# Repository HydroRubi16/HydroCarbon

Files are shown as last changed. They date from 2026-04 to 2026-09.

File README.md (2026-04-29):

# HydroCarbon
This is my custom built 4040/4020 Trident. I will update this over the next few weeks with all my files I used to build my printer..

<!--<img src="https://github.com/HydroRubi16/HydroCarbon/blob/main/images/Trident%20Doom%20front%20angle.png">  -->

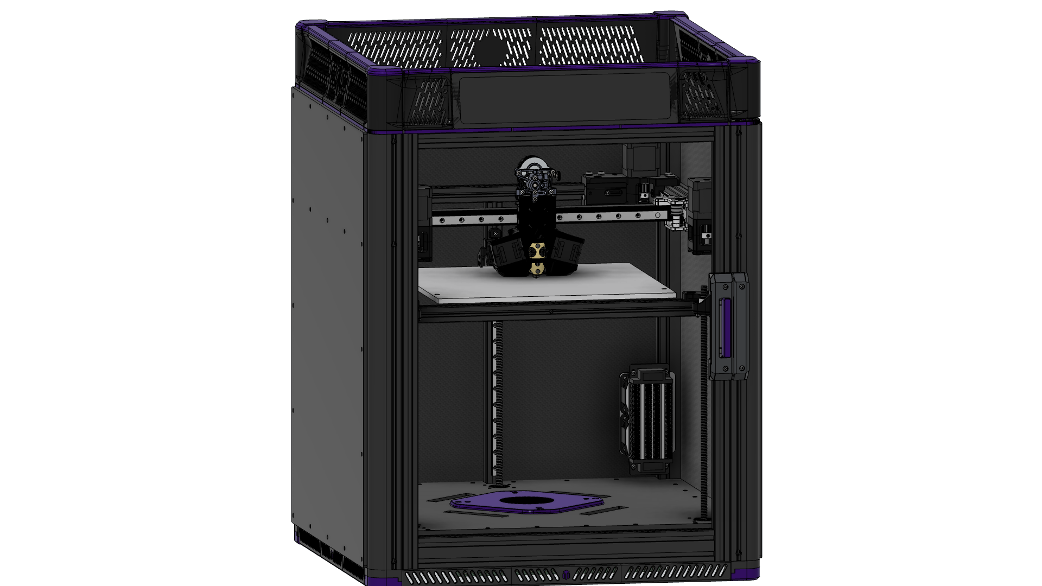
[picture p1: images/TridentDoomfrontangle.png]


This is my latest build, based on all the things I have learned from other builds. I really wanted to build a higher performance printer that looks good. In using the stock extrusion lengths you ‘lose’ 20mm going with 4040 extrusions and 28mm with Trinity, which is why I’m using the 300 Cube length corners (550mm) with standard 300mm lead screw steppers — this should still allow me 250mm Z travel (Actually 238mm right now..). I drilled additional hole in the round corners to allow 3 fasters to be used with 4040 sides and back. For the panels there will be a stack of 3.5mm carbon fiber, 10mm adhesive foam insulation, 5mm structurer panel. Yes, carbon fiber is a bit crazy here, but I got a killer deal on 3.5mm … apparently no one uses it, so it was cheaper than PC panels.

**Frame:**  
Trident Doom corners by LDO (300 Cube)  
4040 on bottom sides/back  
2040 on top and bottom front  
Dual 2040 on Y  
Corner braces wherever possible  

**Gantry:**  
Printed Monolith AWD 10mm (3DXTech EZPCCF)  
(Like everyone else, I’m going CNC as soon as it’s available)  
Sheet metal XY Joints  
Carbonara X Beam  
West3D Berserker hybrid ceramic bearings  
10mm EDPM closed loop belts  

**Toolhead:**  
Trinity modded for 10mm belts  
Chube Compact  
Sherpa Mini  

**Motors:**  
LDO-42STH48-2504AH(S45R)  
LDO-42STH40-1684L300E  

**Rails:**  
BST for Z  
Hiwin for Y  
Airtac for X  
GPL-226 Lube  

**Electronics:**  
Octopus Max EZ MCU  
EZ5160RGB drivers for X/Y  (48v)  
EZ2209 drivers for Z  (24v)  
Dragon Dinghy expansion board  
Waveshare USB Hub  
Phoenix Contact distribution block  
Spicy Meatball 500W heater  

**Skirts:**  
Top skirts - [Darkmatter Skirts](https://github.com/MasturMynd/Doom-Stuff/tree/main/Darkmatter-Skirts)  
Short skirts on the bottom by Brazuka and Komikaze

**Panels and insulation:**  
4.7mm structure panels on Sides/Back  
6.3mm bottom panel with motor mounts and integrated filter  
ACM top plate  
10mm and 15mm adhesive foam insulation  
3.5mm carbon fiber panels for interior  

**Goal: Gucci as fuck**

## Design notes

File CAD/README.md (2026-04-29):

# CAD coming soon......

## Frame BOM
LDO Trident DoomCube Corner Kit (300 cubed)  

| Misumi Part Number | Quantity | Location |
| --- | --- | --- |
| HFSB5-4040-420 | 3 | bottom sides/bottom back |
| HFSB5-2040-420 | 6 | top sides/top back/bottom front/Y |
| HFSB5-2020-420 | 2 | top front/bed mount |
| HFSB5-2020-360 | 1 | Z vertical |
| HFSB5-2020-290 | 1 | rear gantry |
| HFSB5-2020-282 | 1 | bed mount |
| HFSB5-2020-378 | 1 | door top |
| HFSB5-2040-378 | 1 | door bottom |
| HFSB5-2020-550 | 2 | door uprights |

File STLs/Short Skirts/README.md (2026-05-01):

# Short Skirts
Because who doesn't love short skirts?  
by Brazuka and Komikaze  

These Skirts are made exclusively for 300 Tridents or similar machines, with rounded vertical corners and top mounted electronics. You could definitely adapt other feet
to the design, but it's inteded to be used with [Hula Feet](https://github.com/thrutheframe/HULA_Voron/tree/main) (using the Switchwire plate). This can be used with either a RGB strip light or Disco on a stick. There are files for 10mm and 12mm strip lights, so choose which one fits your application. The center short skirt has the ability to also insert a neopixel. Inserts can be omitted, or printed in clear PETG or ABS, or some prefer white PLA.  
  
The feet have passage ways for running wiring up the LDO rounded corners; Please use PET sleeving for your wiring. It will rattle arround like a MF'r if you don't. 

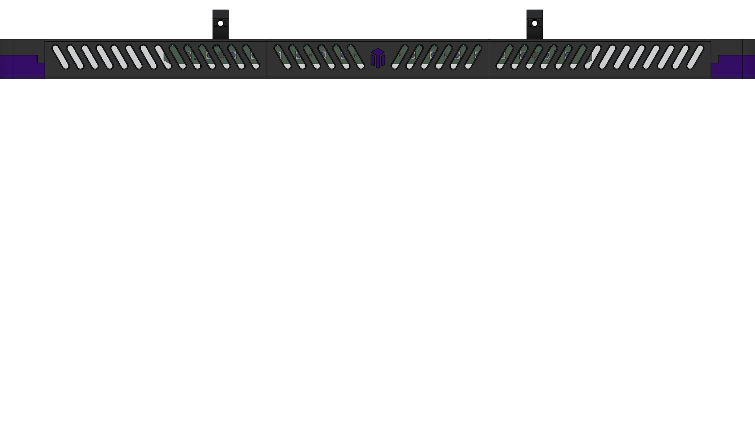
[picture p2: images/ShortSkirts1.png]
  

CAD coming sooooon...

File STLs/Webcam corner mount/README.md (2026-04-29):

# Trident corner mount web cam  

This is my web cam mount design I created for my Trident build. It's made for the Arducam, or anything of similar size-
https://www.amazon.com/dp/B0829HZ3Q7?ref_=ppx_hzsearch_conn_dt_b_fed_asin_title_7

There is a channel on the outside of the perimeter for running chamber light wiring or thermistors. The larger diameter hole is for running wiring to a top mounted electronics bay. The Cam holder is attached to the cam corner mount via 2x m3 heatserts and appropriate fasteners.

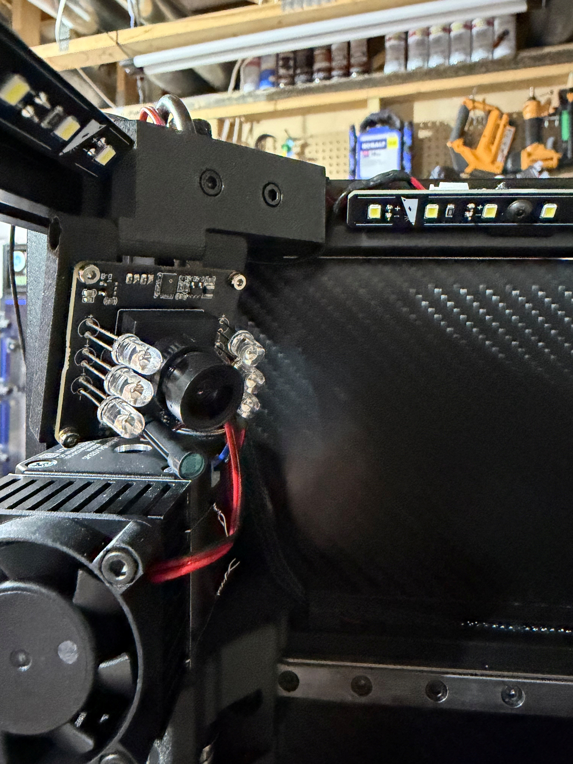
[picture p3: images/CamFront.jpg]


and a view from the top....  
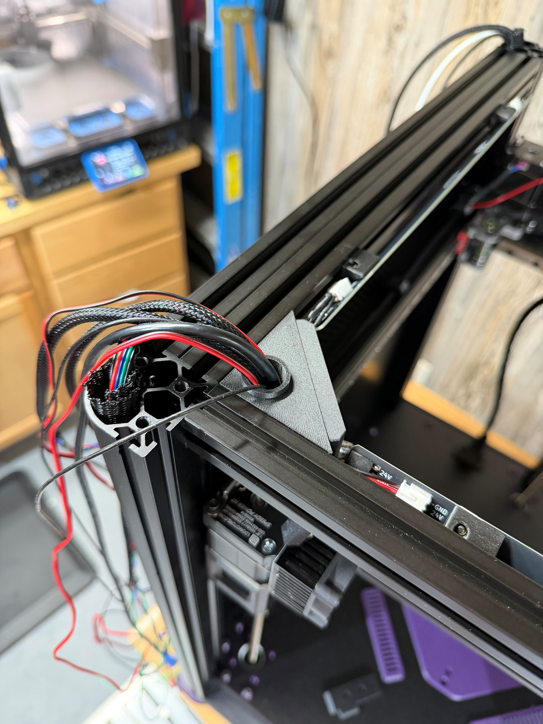
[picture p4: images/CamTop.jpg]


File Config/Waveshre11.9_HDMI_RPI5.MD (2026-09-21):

# How to install an 11.9" Waveshare HDMI display with an RPI5 using Klipperscreen
  
1. Install the HDMI screen, attach USB power, USB Touch, and HDMI to the first HDMI port (closest to USB-C)  
  
2. SSH into the PI  
```
sudo nano /boot/firmware/cmdline.txt
```  

add the following at the very end:  

```
video=HDMI-A-1:1480x320@60,rotate=90
```
	
3. Install Klipperscreen. When prompted for x11 or Wayland, choose W for Wayland  
  
4. Klipperscreen installs Cage, and I could only get Weston to work, so uninstall Cage and install Weston:  
	Uninstall Cage:  
```
sudo systemctl stop KlipperScreen
```

```
sudo apt remove cage
```

Install Weston:  

```
sudo apt install Weston seatd
```

5. Verify HDMI port and connection status  

```
grep -H . /sys/class/drm/card*-*/status | grep :connected
```

Should look like:```/sys/class/drm/card1-HDMI-A-1/status:connected```
		
6. Update INI file  
	
```
sudo nano ~/.config/weston.ini
```
	
Add the following:  

```
[output]  
name=HDMI-A-1  
transform=rotate-90
```

7. Reboot. Klipperscreen should be oriented correctly. Changing the rotating in the Weston.ini file also appears to change the touch overlay, as well.  
```
sudo reboot
```

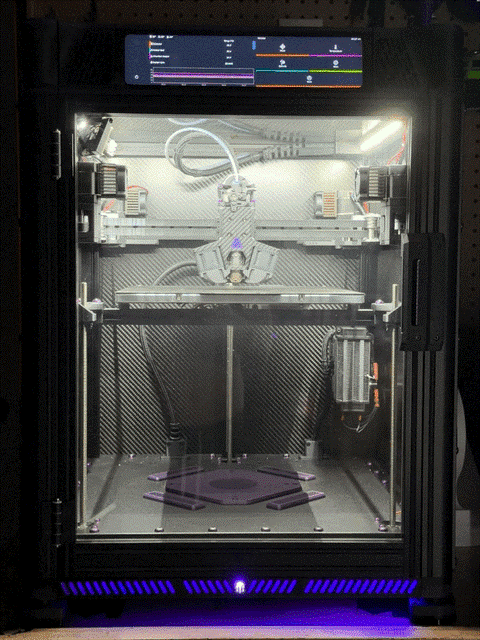
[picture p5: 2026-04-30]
images/HydroCarbon.gif

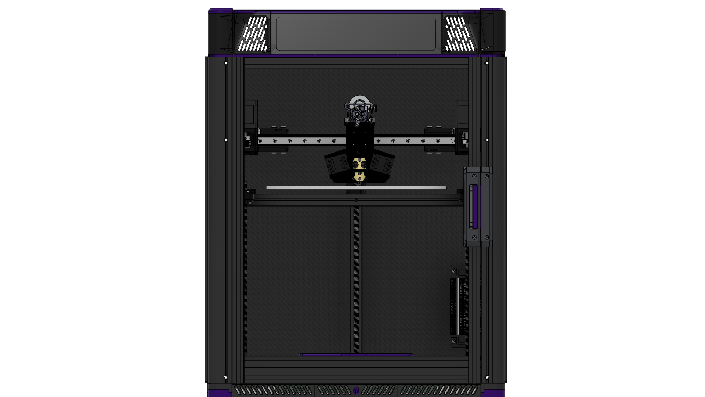
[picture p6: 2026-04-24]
images/TridentDoom.png

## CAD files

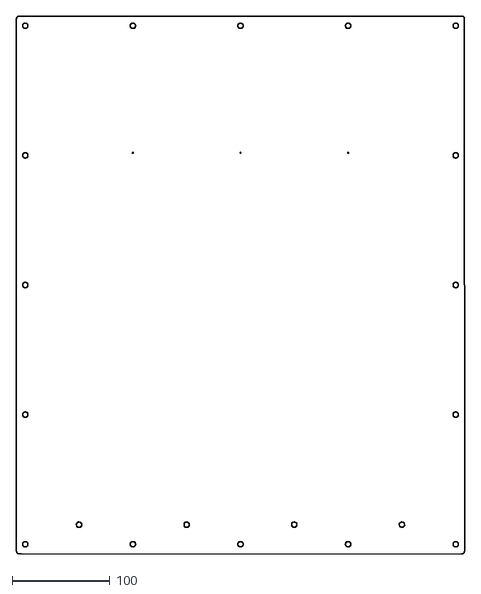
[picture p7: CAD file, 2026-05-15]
DXFs/Side_back_panel_small_hole_minus1.dxf
458.0 x 550.0

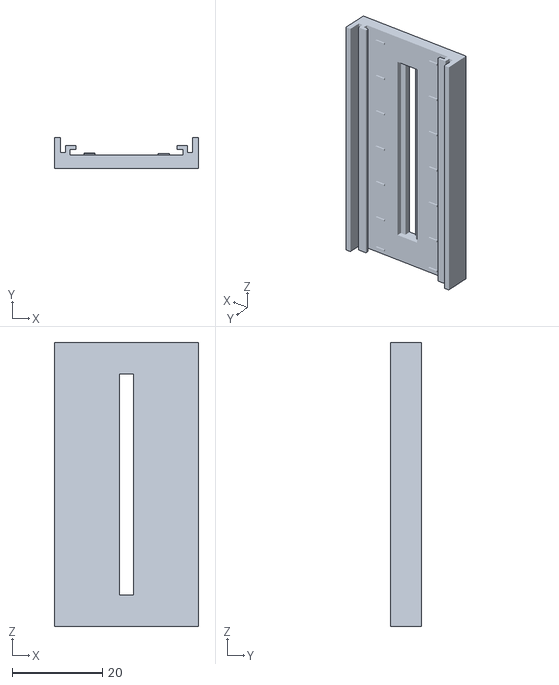
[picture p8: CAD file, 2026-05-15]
STLs/EMS Mounts/PTFIX_DC_EMS.stl
32.0 x 6.99 x 63.0

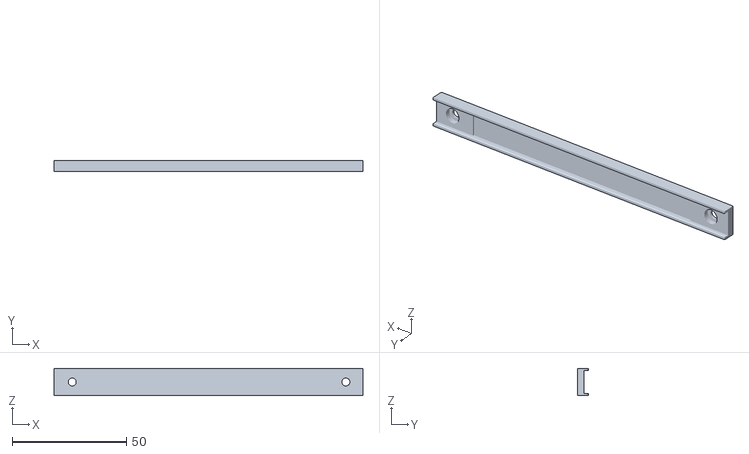
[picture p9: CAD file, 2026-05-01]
STLs/Short Skirts/StripHolder10mm.stl
135.5 x 5.00 x 12.0

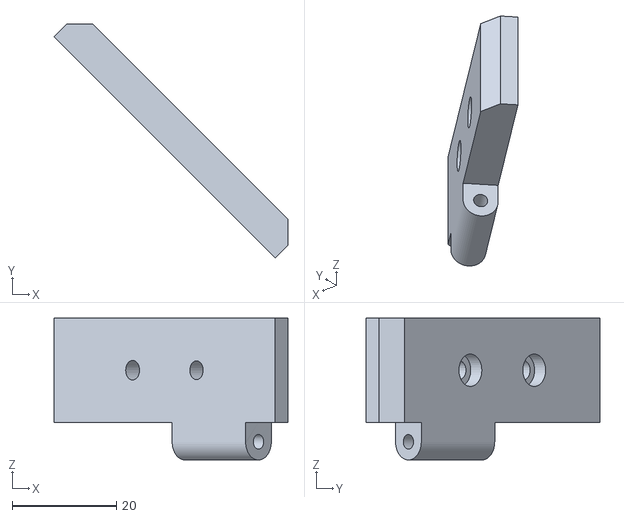
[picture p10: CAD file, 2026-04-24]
STLs/Webcam corner mount/cam holder.stl
44.8 x 44.8 x 27.2

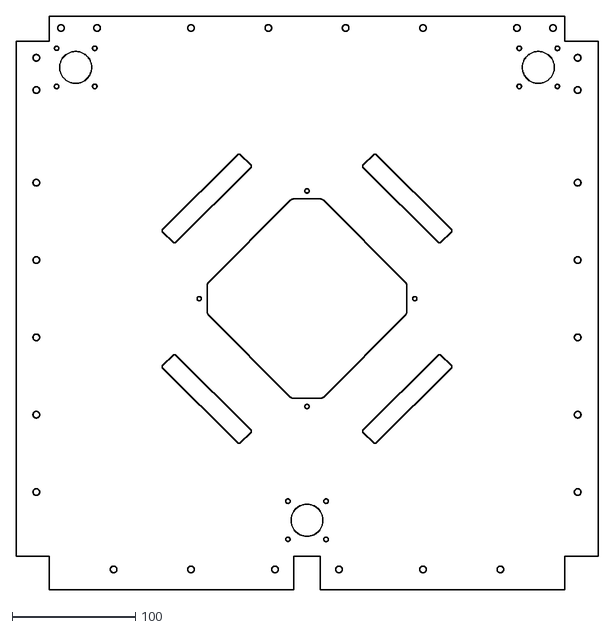
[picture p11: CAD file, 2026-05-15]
DXFs/Trident bottom panel with filter.dxf
473.0 x 466.0

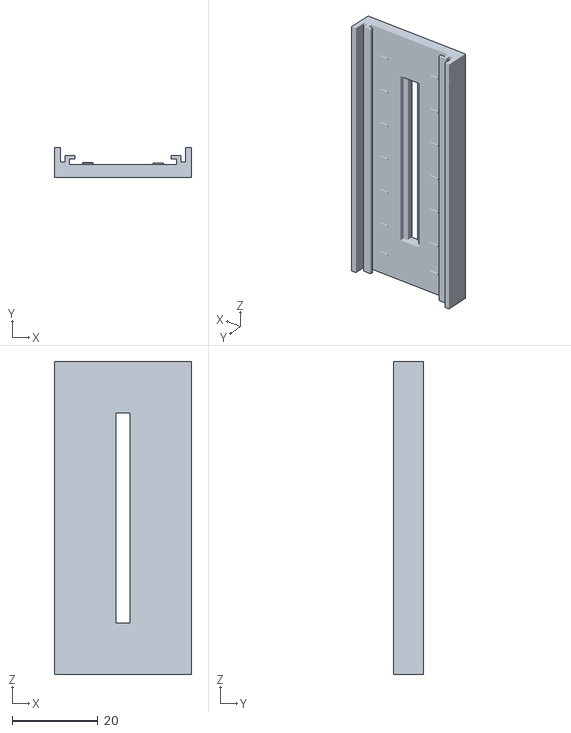
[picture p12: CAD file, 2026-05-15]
STLs/EMS Mounts/PTFIX_120v_EMS.stl
32.0 x 6.99 x 73.0

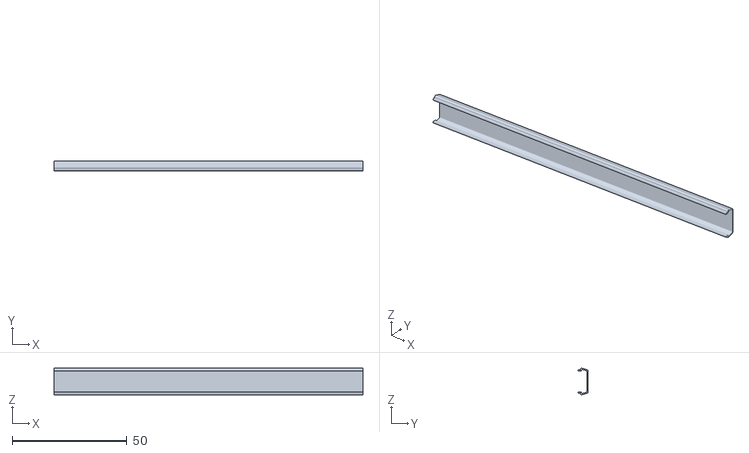
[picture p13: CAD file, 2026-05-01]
STLs/Short Skirts/StripDiffuser10mm.stl
134.5 x 4.32 x 11.7

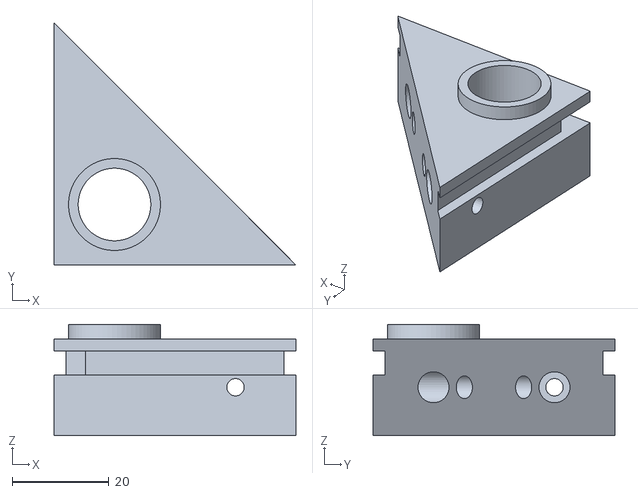
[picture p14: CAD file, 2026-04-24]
STLs/Webcam corner mount/cam corner mount.stl
50.0 x 50.0 x 23.0

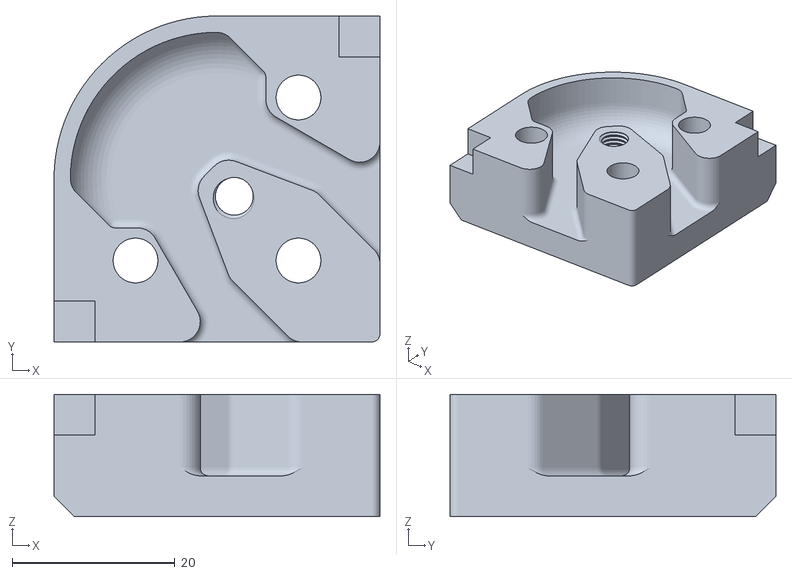
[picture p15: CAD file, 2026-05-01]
STLs/Short Skirts/CornerBottomFoot_v2.stl
40.0 x 40.0 x 15.0

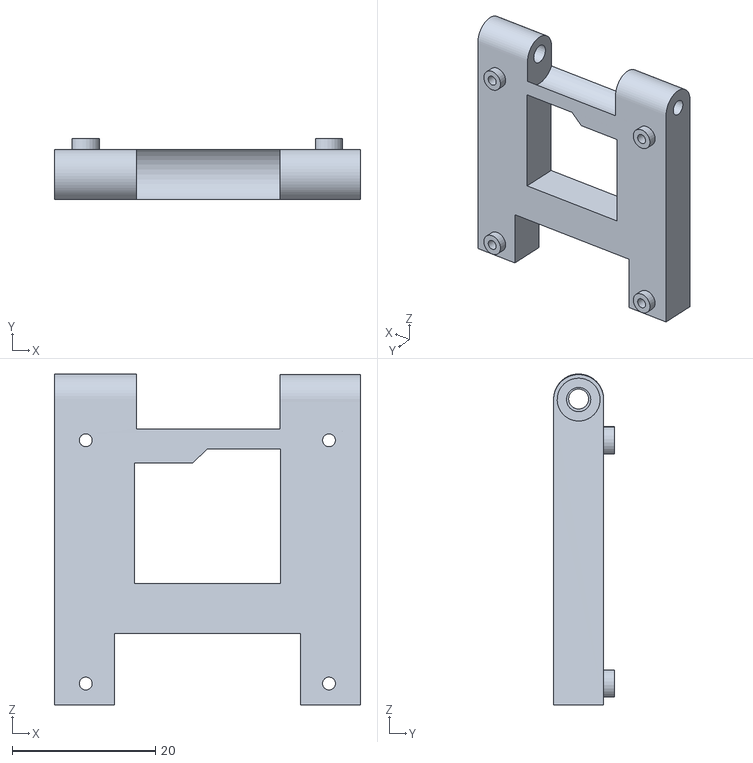
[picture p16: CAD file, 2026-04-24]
STLs/Webcam corner mount/cam mount.stl
42.8 x 8.50 x 46.3

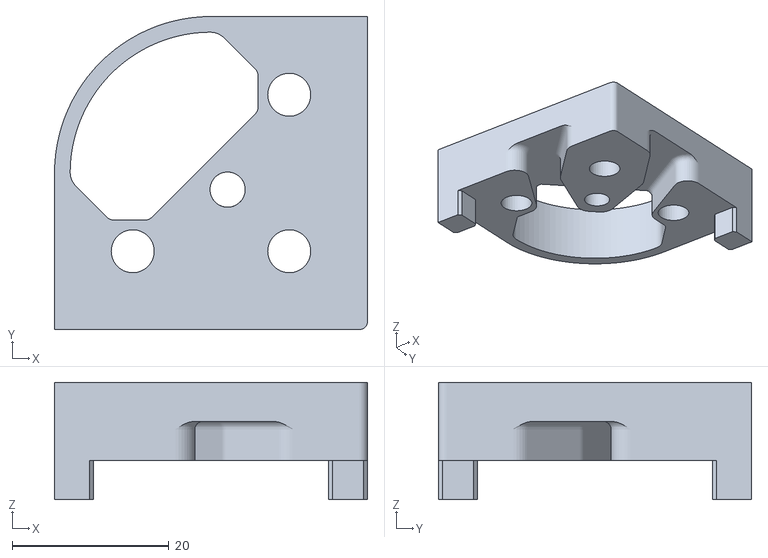
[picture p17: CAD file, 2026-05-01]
STLs/Short Skirts/CornerTopFoot_v2.stl
40.0 x 40.0 x 15.0

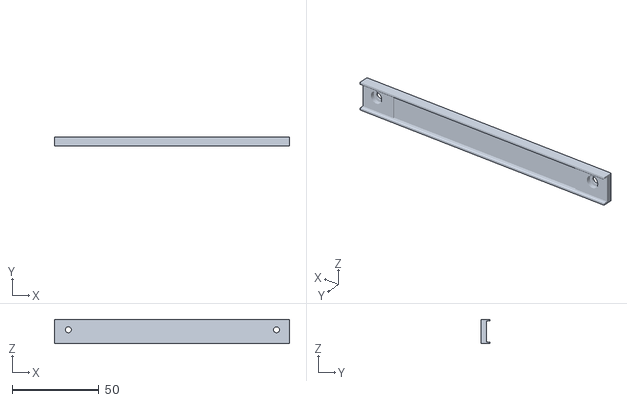
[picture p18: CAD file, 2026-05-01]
STLs/Short Skirts/StripHolder12mm.stl
135.5 x 5.00 x 14.0

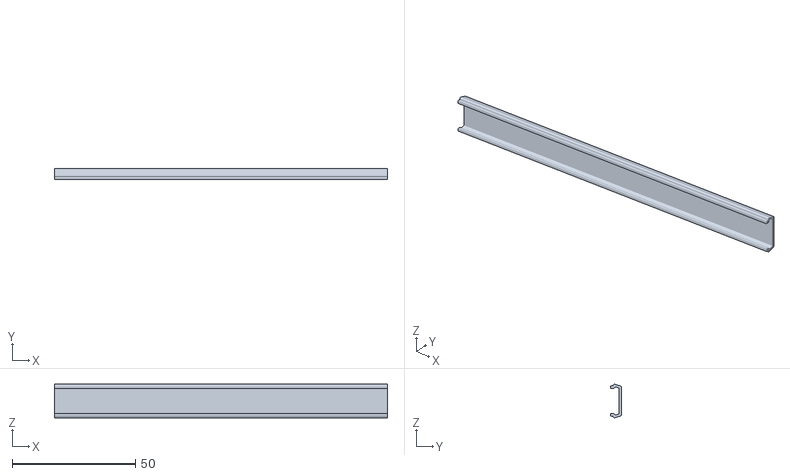
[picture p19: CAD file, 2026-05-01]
STLs/Short Skirts/StripDiffuser12mm.stl
135.0 x 4.32 x 13.7

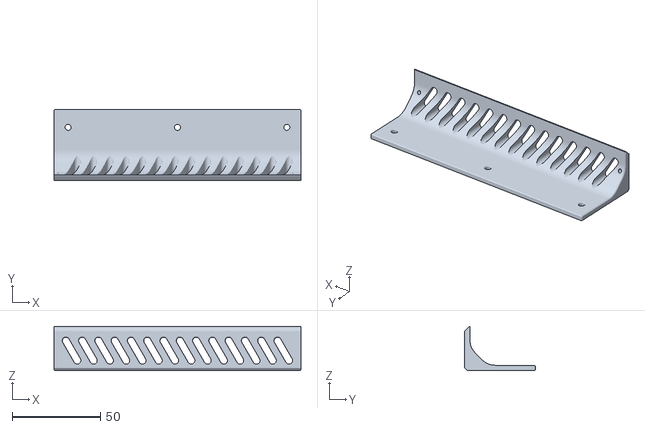
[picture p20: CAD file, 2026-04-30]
STLs/Short Skirts/ShortSkirt_L.stl
140.0 x 40.0 x 25.0

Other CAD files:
STLs/Short Skirts/NeoPixelHolder.stl
STLs/Short Skirts/Diffuser_L.stl
STLs/Short Skirts/ShortSkirt_C.stl
STLs/Short Skirts/Diffuser_C.stl
STLs/Short Skirts/Diffuser_R.stl
STLs/Short Skirts/NeoPixelDiffuser.stl
STLs/Short Skirts/ShortSkirt_R.stl

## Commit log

2026-04-24 Add files via upload
    initial upload
    [cam corner mount.stl, cam holder.stl, cam mount.stl]
2026-04-24 Rename cam corner mount.stl to Webcam corner mount/cam corner mount.stl
    [cam corner mount.stl]
2026-04-24 Rename cam holder.stl to webcam corner mount/cam holder.stl
    [cam holder.stl]
2026-04-24 Rename cam mount.stl to Webcam corner mount/cam mount.stl
    [cam mount.stl]
2026-04-29 changing folder structure
    [cam corner mount.stl, cam holder.stl, cam mount.stl]
2026-04-30 Rename Hydrorubi's short skirts doom with Lights v1_Hydrorubi's short skirts doom with Lights v1_Body3.stl to Diffuser_L.stl
    [Diffuser_L.stl]
2026-04-30 Rename Hydrorubi's short skirts doom with Lights v1_Hydrorubi's short skirts doom with Lights v1_Body4.stl to Diffuser_R.stl
    [Diffuser_R.stl]
2026-04-30 Rename Hydrorubi's short skirts doom with Lights v1_Hydrorubi's short skirts doom with Lights v1_Body5.stl to Diffuser_C.stl
    [Diffuser_C.stl]
2026-04-30 Rename Hydrorubi's short skirts doom with Lights v1_Hydrorubi's short skirts doom with Lights v1_Body6.stl to NeoPixelHolder.stl
    [NeoPixelHolder.stl]
2026-04-30 Rename Hydrorubi's short skirts doom with Lights v1_Hydrorubi's short skirts doom with Lights v1_doo mini skirt_1_Body1.stl to ShortSkirt_L.stl
    [ShortSkirt_L.stl]
2026-04-30 Rename Hydrorubi's short skirts doom with Lights v1_Hydrorubi's short skirts doom with Lights v1_doo mini skirt_mid_1_Body1.stl to ShortSkirt_C.stl
    [ShortSkirt_C.stl]
2026-04-30 Rename Hydrorubi's short skirts doom with Lights v1_Hydrorubi's short skirts doom with Lights v1_doo mini skirt_mid_1_Body2.stl to NeoPixelDiffuser.stl
    [NeoPixelDiffuser.stl]
2026-04-30 Rename Hydrorubi's short skirts doom with Lights v1_Hydrorubi's short skirts doom with Lights v1_doo mini skirt_mirror_1_Body1.stl to ShortSkirt_R.stl
    [ShortSkirt_R.stl]
2026-04-30 Rename Hydrorubi's short skirts doom with Lights v1_Hydrorubi's short skirts doom with Lights v1_passtru wire_2_Body1.stl to CornerFootBottom.stl
    [CornerFootBottom.stl]
2026-04-30 Rename Hydrorubi's short skirts doom with Lights v1_Hydrorubi's short skirts doom with Lights v1_passtru wire_2_Body2.stl to CornerFootUpper.stl
    [CornerFootUpper.stl]
